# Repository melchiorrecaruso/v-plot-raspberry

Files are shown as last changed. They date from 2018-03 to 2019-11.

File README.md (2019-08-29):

# vPlot

vPlot è una stampante verticale, un tipo di stampante che disegna tracciati e figure su una superfice verticale utilizzando due motori e la forza di gravità.

## Requisiti

vPlot utilizza i seguenti componenti:

>- 1x Raspberry Pi 3 Model B board
>- 1x PCA9685 16 channel 12-bit PWM servo motor driver board
>- 1x CNC Shield V3 expansion board
>- 2x DRV8825 stepper motor driver 
>- 2x Stepper motor Nema-17 (min torque 40Ncm)
>- 1x Micro digital servo 
>- 2x Timing belt pulley GT2 20T 5mmn bore
>- 2x Smooth idler pulley with bearings GT2 20T 5mm bore
>- 2x 2,5m GT2 timming belt 
>- 1x 12V/5A power supplier
>- 1x 5V/5A power supplier 
>- 1x Pen holder (buy or print at home with a 3D printer)
>- 2x Motor supports (buy or print at home with a 3D printer)

Per compilare vPlot-Driver e vPlot-Layout occorre installare sulla scheda Raspberry Pi:  

>- [WiringPi library](http://wiringpi.com/download-and-install/)
>- [Lazarus IDE and FreePascal compiler](https://www.lazarus-ide.org/index.php?page=downloads)

## Working principle

Ogni posizione XY del pennino è definita da una coppia di lunghezze A e B.

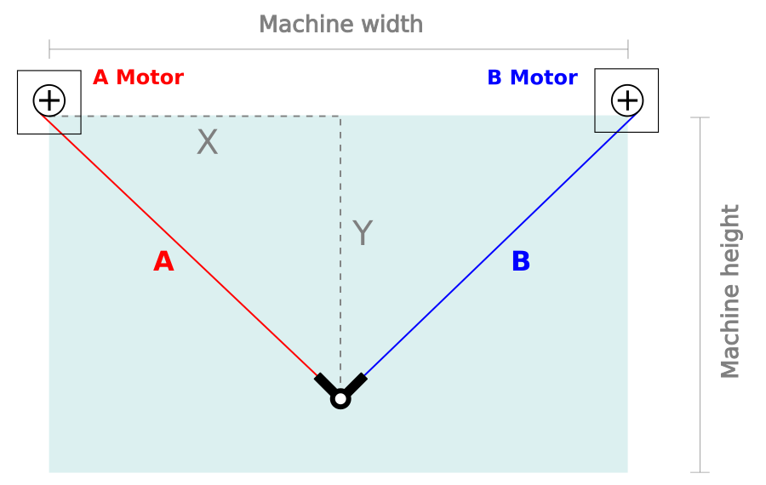
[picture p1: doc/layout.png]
Layout


Per ciascuna posizione del pennino è possibile calcolare tali lunghezze utilizzando il teorema di pitagora:

Equations

Per semplicità costruttiva, solitamente i due motori vengono posizionati alla stessa altezza da terra.

## Working area:

vPlot-Layout permette di calcolare l'area di stampa ottimale in base alla

>- distanza tra i due motori

ed ai seguneti parametri:

>- min rapporto tra tensione cinghia e massa supporto pennino
(default 0.5)
>- max rapporto tra tensione cinghia e massa supporto pennino
(default 1.5)
>- max rapporto tra spostamento pennino ed allungamento cinghia
(default 1.4)

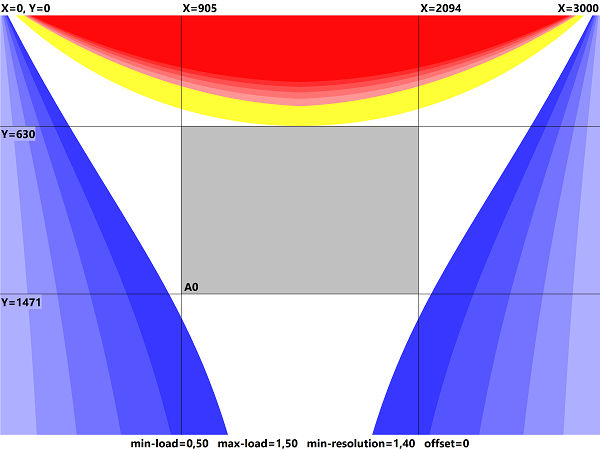
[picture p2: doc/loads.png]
Loads


Nella zona in bianco vengono rispettati tutti e tre i parametri sopra indicati. Nella zona il blu il carico di una delle due cinghie è inferiore al carico minimo ammesso; Nella zona in rosso la tensione di una delle due cinghie è superiore carico massimo ammesso; Nella zona in giallo la risoluzione del plotter è inferiore alla risoluzione minima ammessa. 

In genere, più è grande la distanza tra i due motori più grande è l'area della zona bianca. 

## Before assembling

Next we need to set the maximum current on DRV8825

## Connecting to Raspberry

PCA9685 wiring:

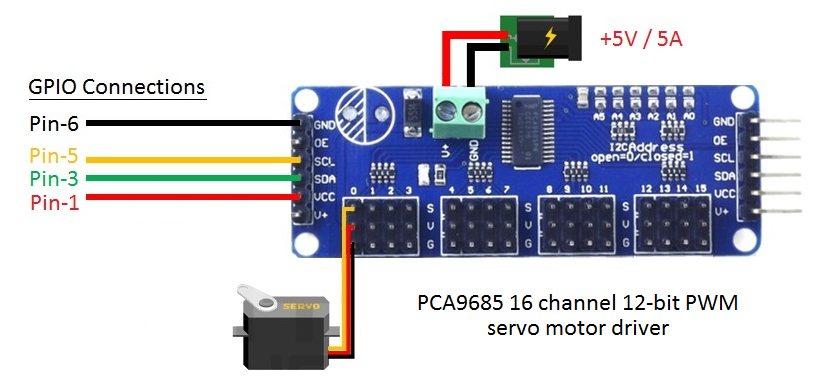
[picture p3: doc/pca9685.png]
pca9685 (https://)
 

CNC Shield wiring:

Nema 17 motors have 200 steps for rotation but by enabling quarters of steps on the Pololu drivers we can obtain up to 800 steps for rotation which allows for much more precision. For doing that add an

cncshield (https://)

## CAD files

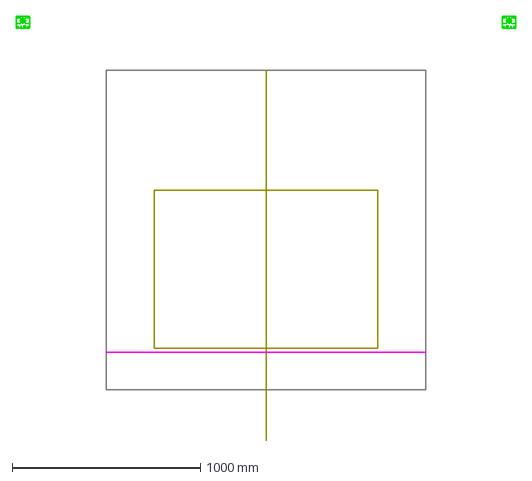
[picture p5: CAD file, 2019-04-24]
hardware/SCHEME.dxf
2654.0 x 2255.5 mm

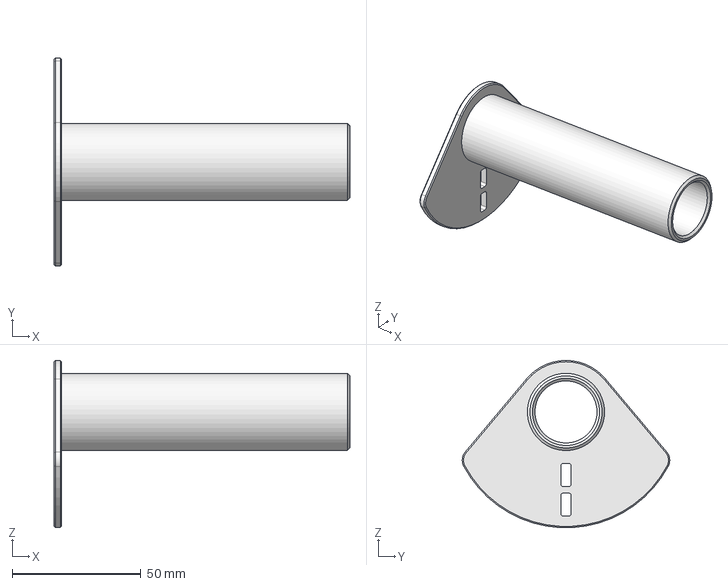
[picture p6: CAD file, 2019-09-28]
hardware/v4.0/vp4009.FCStd
115.0 x 80.7 x 64.9 mm

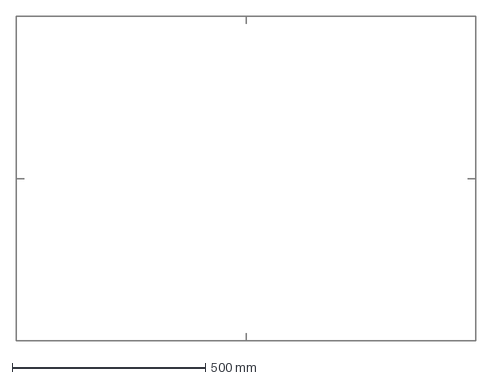
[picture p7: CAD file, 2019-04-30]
test/A0.STEP-2.dxf
1189.0 x 841.0 mm

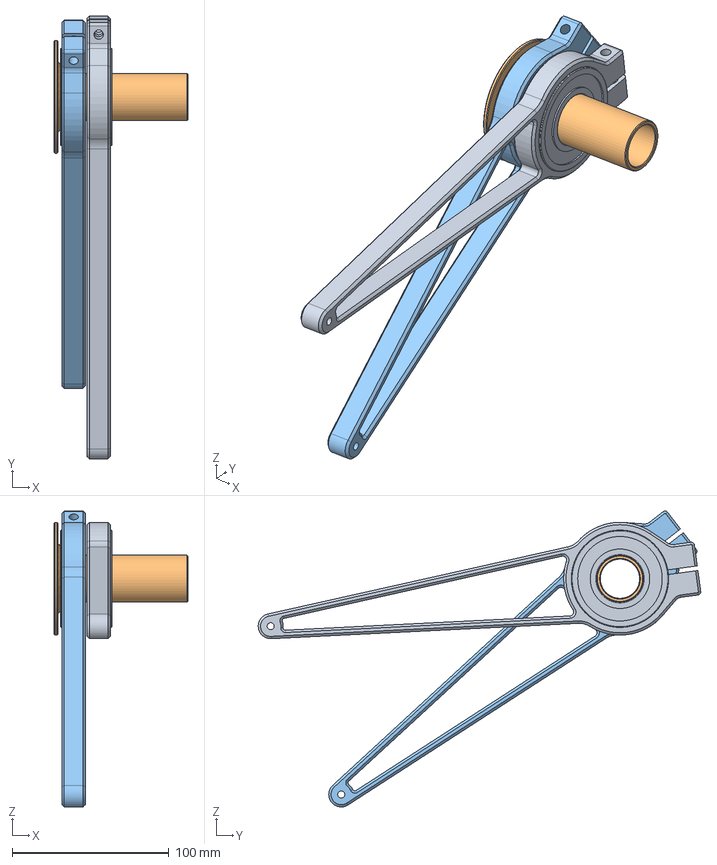
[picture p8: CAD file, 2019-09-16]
hardware/v4.0/vp4000.FCStd
85.5 x 282.5 x 188.9 mm
vp4008_002
vp4009_001
vp4008_001

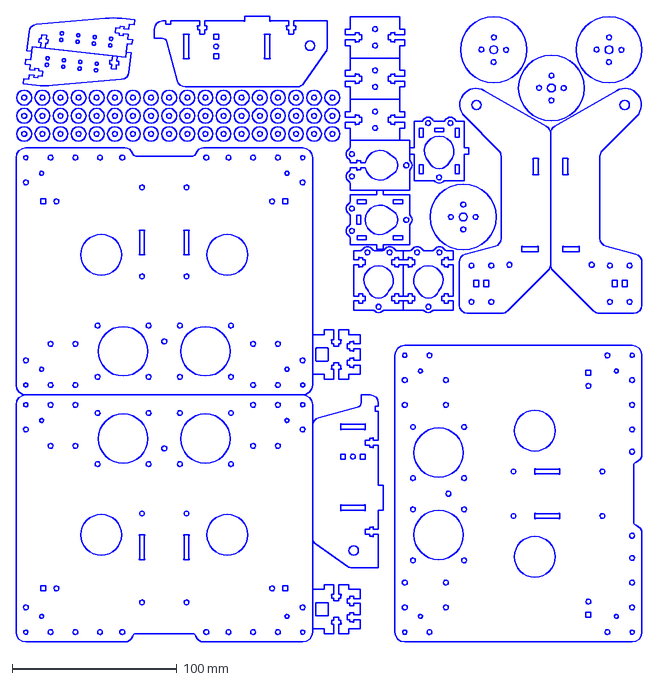
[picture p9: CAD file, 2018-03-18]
hardware/VPLOT2_LASER_3mm.dxf
380.6 x 380.0 mm

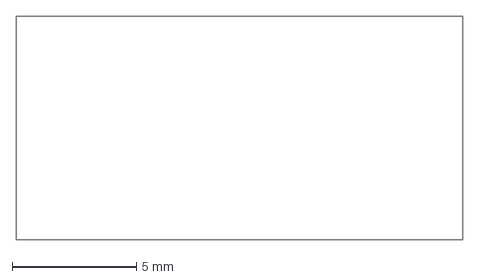
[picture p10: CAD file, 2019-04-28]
test/angle.dxf
18.0 x 9.00 mm

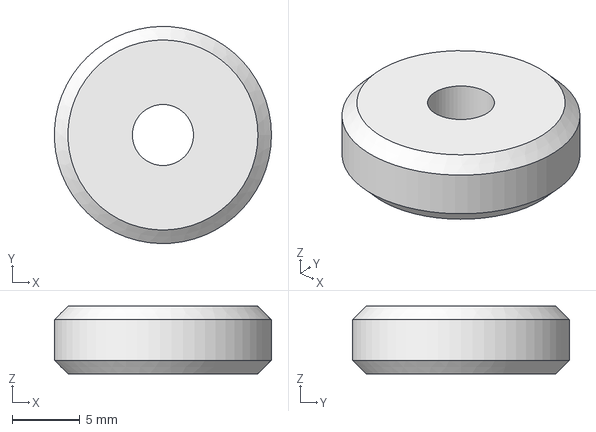
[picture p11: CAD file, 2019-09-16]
hardware/v4.0/vp4005.FCStd
16.0 x 16.0 x 5.00 mm

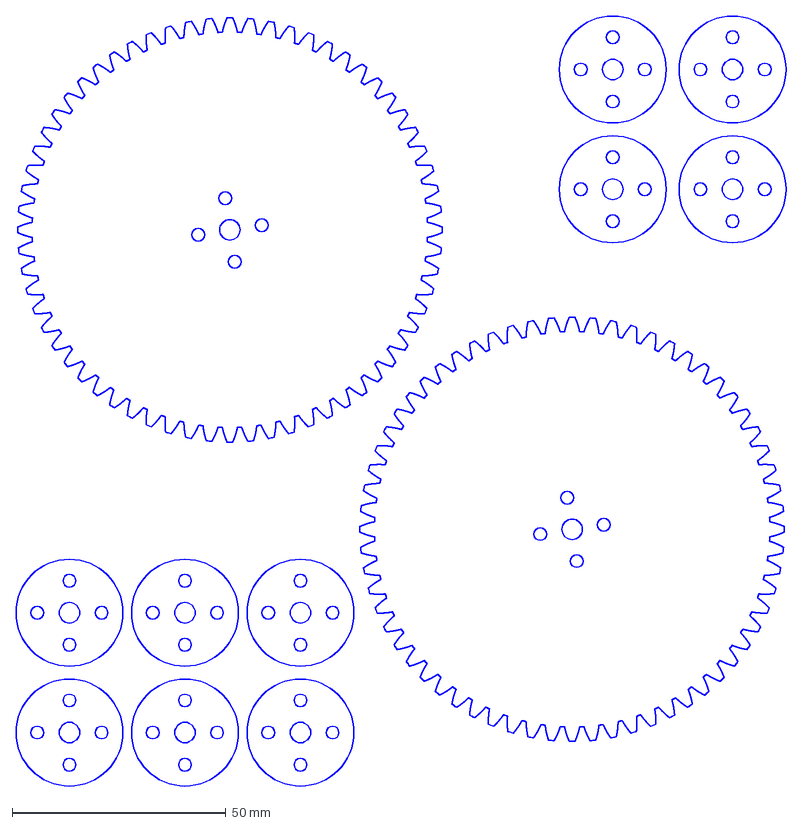
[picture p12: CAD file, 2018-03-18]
hardware/VPLOT2_LASER_4mm.dxf
180.0 x 180.0 mm

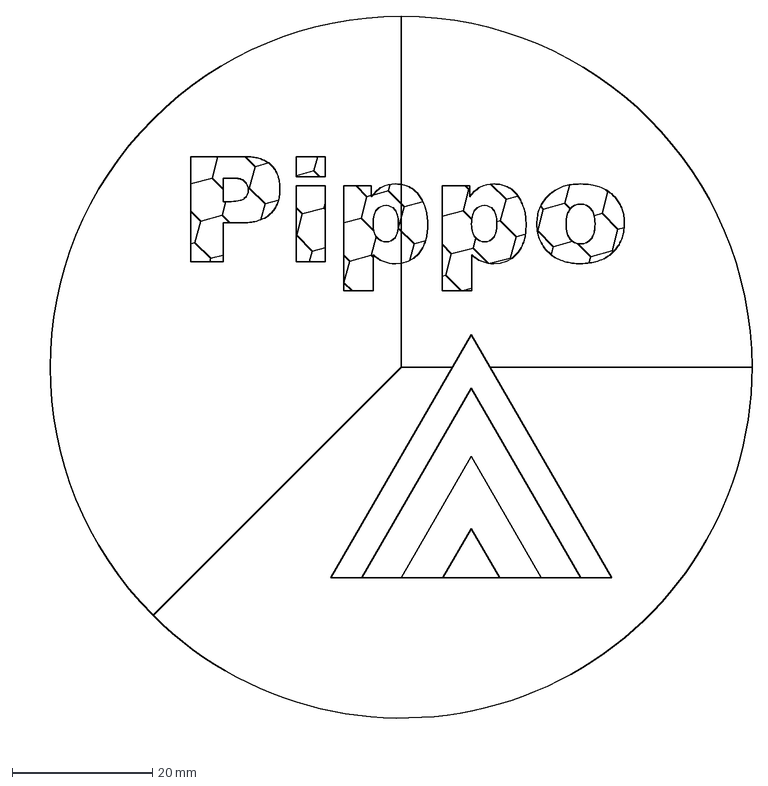
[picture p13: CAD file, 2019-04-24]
test/tratteggio2.dxf
104.9 x 103.9 mm

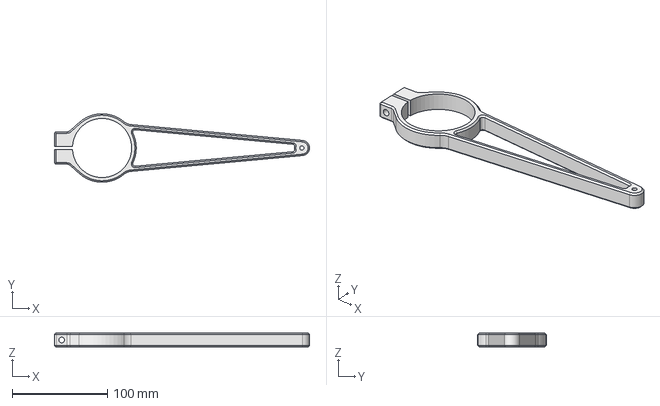
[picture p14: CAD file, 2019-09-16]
hardware/v4.0/vp4003.FCStd
268.0 x 72.0 x 15.0 mm

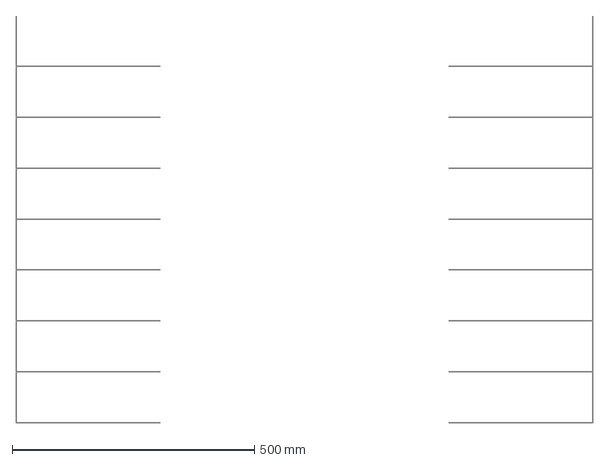
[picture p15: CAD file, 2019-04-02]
test/A0.1.dxf
1189.0 x 839.0 mm

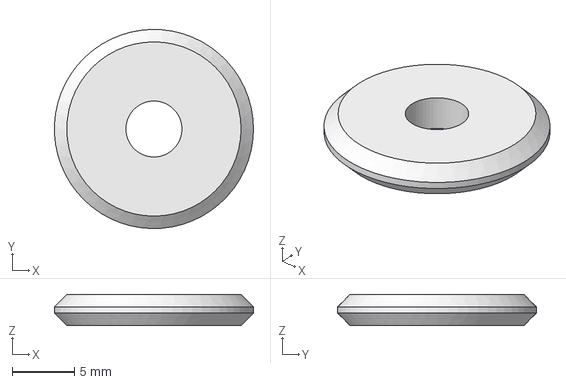
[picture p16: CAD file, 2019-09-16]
hardware/v4.0/vp4004.FCStd
16.0 x 16.0 x 2.50 mm

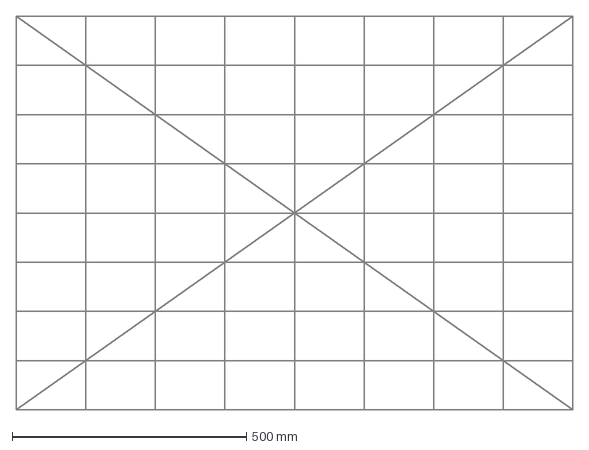
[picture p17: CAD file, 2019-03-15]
test/A0.dxf
1189.0 x 841.0 mm

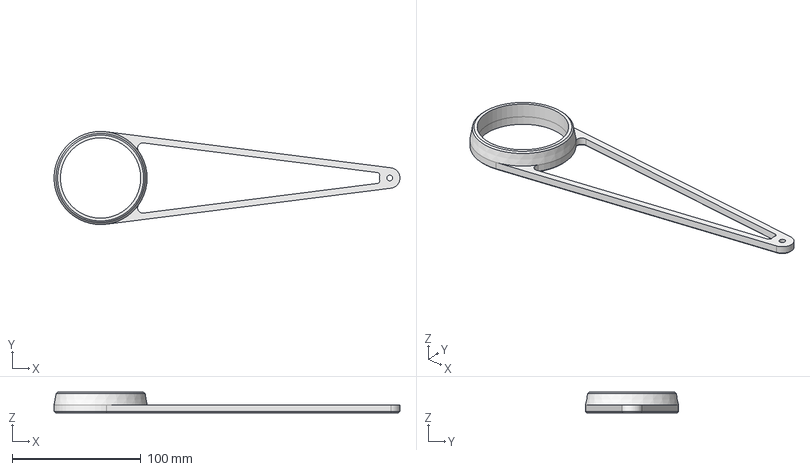
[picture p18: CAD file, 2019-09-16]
hardware/v4.0/vp4002.FCStd
269.2 x 72.5 x 16.0 mm

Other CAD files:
test/scudo.dxf
hardware/v4.0/vp4008.FCStd
test/dv.dxf
hardware/v4.0/vp4007.FCStd
hardware/v3.0/00.FCStd
hardware/v3.0/01.FCStd
hardware/v3.0/02.FCStd
hardware/v3.0/03.FCStd
hardware/v3.0/04.FCStd
hardware/v3.0/05.FCStd
hardware/v3.0/06.FCStd
hardware/v3.0/07.FCStd
hardware/v3.0/08.FCStd
hardware/v3.0/09.FCStd
hardware/v4.0/vp4001.FCStd
hardware/v4.0/vp4006.FCStd
test/A0.STEP-1.dxf
test/A1.dxf
test/A2.dxf
test/DimRad.dxf
test/bike.dxf
test/calendarioA0-clean.dxf
test/calendarioA0.dxf
test/edolito - Copia.dxf
test/ele.dxf
test/freedom-1.dxf
test/freedom-2.dxf
test/freedom-3.dxf
test/freedom-clean.dxf
test/freedom.dxf
test/mau.dxf
test/pippo.dxf
test/tratteggio-step1.dxf
test/tratteggio-step2.dxf
test/tratteggio.dxf

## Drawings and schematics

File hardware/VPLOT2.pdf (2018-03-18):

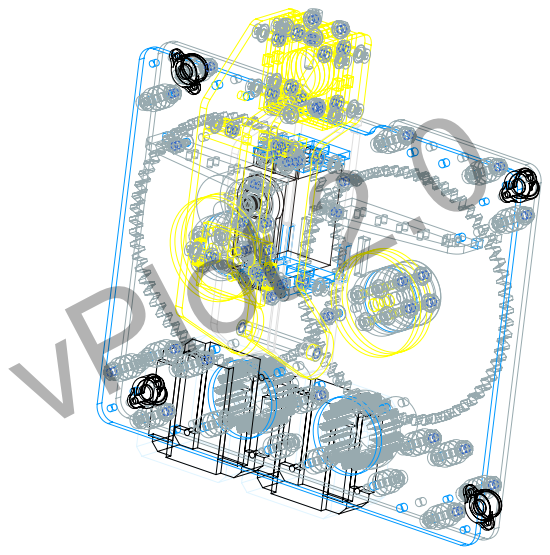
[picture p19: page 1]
vPlot 2.0

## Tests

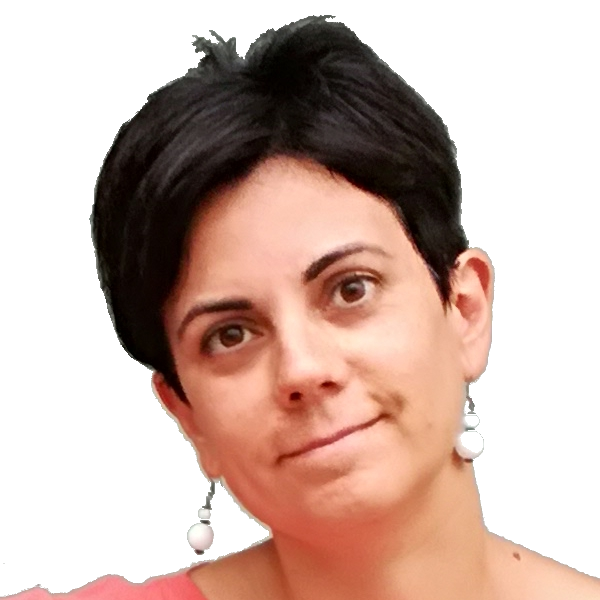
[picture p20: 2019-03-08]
test/ele2.png

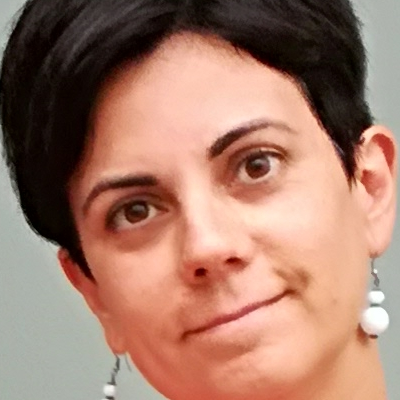
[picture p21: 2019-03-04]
test/ele.png

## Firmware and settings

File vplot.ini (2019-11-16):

[LAYOUT]
L0.X=+0
L0.Y=+2200
L1.X=+2566
L1.Y=+2202

L8.X=1283
L8.Y=1338
LY-1=-0.5
LY-2=-15

[X-AXIS]
MIN=400
MAX=4000
DEC=200
INC=800
DELAY=400
DIR=0
RADIUS=6.0
RATIO=0.01238

[Y-AXIS]
MIN=400
MAX=4000
DEC=200
INC=800
DELAY=400
DIR=1
RADIUS=6.0
RATIO=0.01238

[Z-AXIS]
MIN=214
MAX=200
DEC=2
INC=2
DELAY=35000
DIR=1
RADIUS=0
RATIO=0

[SPACE-WAVE]
00.X=+0.0
00.Y=+0.0
01.X=+0.0
01.Y=+1.25
02.X=-0.0
02.Y=+0.0
03.X=-0.0
03.Y=+0.0
04.X=+0.0
04.Y=+1.25
05.X=+0.0
05.Y=+0.0
06.X=-0.0
06.Y=+0.0
07.X=+0.0
07.Y=+1.25
08.X=+0.0
08.Y=+0.0
DXMAX=594.5
DYMAX=420.5
SCALE=0.992
ON=1

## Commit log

2018-03-18 Hardware dxf for laser cut.
    [VPLOT2_LASER_3mm.dxf, VPLOT2_LASER_4mm.dxf]
2018-03-18 Updated test files
    [dv.dxf]
2018-03-18 Updated dv test
    [dv.dxf]
2018-03-18 Update test dv
    [dv.dxf]
2018-03-18 Added test bike.dxf
    [bike.dxf]
2018-03-18 Updated test bike
    [bike.dxf]
2018-03-22 New timer functions
2018-04-28 Added new test
    [freedom.dxf]
2018-04-28 Updated test
    [freedom.dxf]
2018-05-01 Update debug switch
2018-05-01 Updated test freedom
    [freedom-1.dxf, freedom-2.dxf]
2018-05-01 Updated freedom test
    [freedom-1.dxf, freedom-3.dxf, freedom.dxf]
2018-05-27 Updated tests
    [freedom.dxf]
2018-05-29 Added A0.dxf
    [A0.dxf]
2018-06-02 Update driver.step routine
2018-06-07 extended driver modes
2018-07-04 new A0-STEP-1
    [A0.STEP-1.dxf]
2018-07-05 Update tests
    [A0.STEP-1.dxf]
2018-07-08 driver update
2018-09-02 updated test folder
    [freedom.dxf]
2018-10-07 driver fixes
2018-10-13 some fixes
    [ele.dxf]
2018-10-17 many changes
    [SCHEME.dxf]
2018-10-28 new test
    [calendarioA0.dxf]
2018-10-28 new features
    [calendarioA0-clean.dxf]
2018-11-02 units cleaning
    [calendarioA0.dxf]
2018-11-25 added layers
    [DimRad.dxf, calendarioA0.dxf, dv.dxf]
2018-12-20 last update
    [A0.dxf, SCHEME.dxf]
2019-01-28 new driver class
2019-01-28 driver fix
2019-02-02 scudo added
    [scudo.dxf]
2019-03-15 updated A0 test
    [A0.dxf]
2019-04-02 added A0.1 TEST
    [A0.1.dxf]
2019-04-24 new version
    [SCHEME.dxf, tratteggio2.dxf]
2019-04-27 math routines
    [angle.dxf]
2019-08-21 Hardware v3.0
    Added hardware v3.0
    [00.FCStd, 01.FCStd, 02.FCStd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]
2019-08-21 Fixes
    Fixed bug in sketcher, some updates.
    [vplot.ini]
